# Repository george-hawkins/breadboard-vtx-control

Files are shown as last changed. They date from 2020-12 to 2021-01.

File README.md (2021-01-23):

Breadboard SmartAudio control via OpenTX
========================================

This project is about creating a breadboard setup where a standard STM32 Nucleo development board acts as a flight controller that enables a transmitter, running OpenTX, to control a SmartAudio video transmitter via an FrSky X-series receiver.

Once set up, you can use a LUA script on your transmitter to change the band etc. on the VTX.

Parts used:

* [Nucleo F722ZE](https://www.st.com/en/evaluation-tools/nucleo-f722ze.html) development board.
* [FrSky X8R](https://www.frsky-rc.com/product/x8r/) receiver (RX).
* [Eachine TX805](https://www.eachine.com/Eachine-TX805-5_8G-40CH-25-or-200-or-600-or-800mW-FPV-Transmitter-TX-LED-Display-Support-OSD-or-Pitmode-or-Smart-Audio-RP-SMA-Female-p-1234.h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) video transmitter (VTX).
* [Eachine 1000TVL](https://www.eachine.com/Eachine-1000TVL-1-3-CCD-110-Degree-2.8mm-Lens-Mini-FPV-Camera-NTSC-PAL-Switchable-p-357.html) FPV camera.
* [12V power supply](https://www.reichelt.com/de/en/eco-friendly-plug-in-power-supply-unit-12-v-1500-ma-2-5-mm-snt-1500-12v-2-5-p108993.html) (plus barrel jack to terminal block [adapter](https://www.adafruit.com/product/368)).

All the work below was done using a computer running Ubuntu, but it should be easy enough to adapt things for Mac or Windows.

Wiring
------

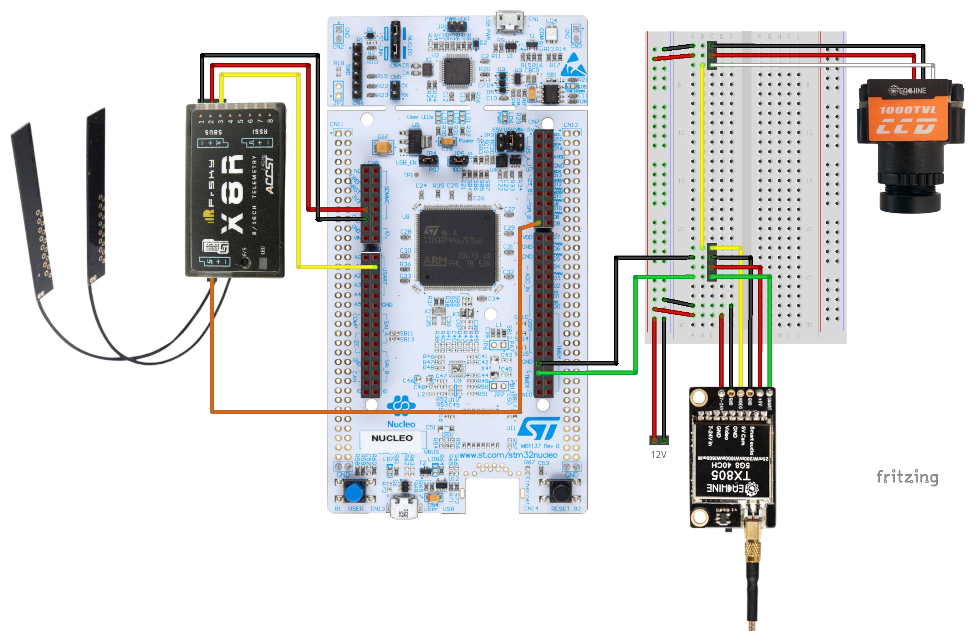
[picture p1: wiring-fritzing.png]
wiring with Fritzing


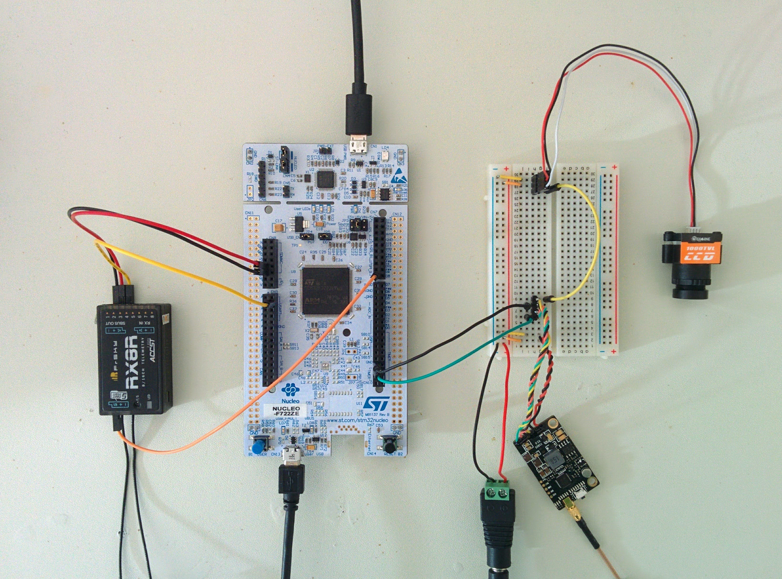
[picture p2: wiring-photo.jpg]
wiring photo


Setting up the Nucleo board
---------------------------

The NUCLEO F722ZE has two USB ports - one, labeled _CN1_, on the small subboard at one end and one, labeled _CN13_, on the main board at the other end. The small subboard is the builtin [ST-LINK](https://www.st.com/en/development-tools/st-link-v2.html). 

Aside: Oddly, the two USB connectors use different components - the one on the ST-LINK is clearly a micro-USB connector, the other is also a micro-USB but upside-down relative to the other one.

Plug a USB cable into the ST-LINK connector (plugging it into the other one does nothing due to the default jumper settings) - it appears as a USB drive.

The board comes with a pre-installed example application that will flash the red user LED madly, press the button labeled _USER_ to get it to cycle through the other user LEDs.

### Upgrade the ST-LINK firmware

Find the latest ST-LINK upgrader under the [products section](https://www.st.com/en/development-tools/stm32-programmers.html#products) of STM32 Programmers page. At the time of writing, it was [STWS-LINK007](https://www.st.com/en/development-tools/stsw-link007.html).

Aside: ST's package naming is quite odd, e.g. at the present time STWS-LINK007 is a package for upgrading the firmware of an ST-LINK device while STSW-LINK009, which sounds like a more recent revision of the same, is in fact a package for the USB drivers needed by Windows to work with an ST-LINK device.

Register with the ST site, download the application and run the upgrader:

    $ cd Downloads
    $ unzip en.stsw-link007_V2-37-26.zip 
    $ cd stsw-link007
    $ cd AllPlatforms
    $ command -v java
    .../bin/java ...
    $ sudo .../bin/java -jar STLinkUpgrade.jar

Note: if you've got the Arduino IDE installed, it includes a version of Java that you can use - you can find `java` in the `java/bin` subdirectory of the IDE's main installation directory.

`sudo` is required so that the application can open USB devices. Once started, the GUI should detect the board, click the _Open in update mode_ and click _Upgrade_ if the _Version_ shown isn't the same as the one shown for _Update to Firmware_.

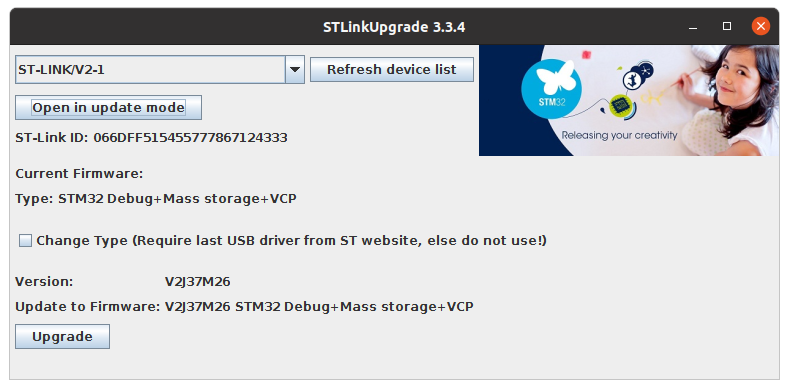
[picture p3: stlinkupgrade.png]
STLinkUpgrade


Note: the ST-LINK upgrader is bundled with the [STM32CubeIDE](https://www.st.com/en/development-tools/stm32cubeide.html) (along with a suitable JRE) - once you've installed and started the IDE, you can find the upgrader as _ST-LINK Upgrade_ in the _Help_ menu.

Installing Betaflight
---------------------

After Betaflight has been installed for the first time, it can be updated via the [Betaflight Configurator](https://github.com/betaflight/betaflight-configurator). But to install it for the first time you have to use the USB drive that shows up when you connect to the ST-LINK subboard via USB (as described above). But first let's build Betaflight locally...

### Building Betaflight

Clone the Betaflight repository:

    $ git clone git@github.com:betaflight/betaflight.git
    $ cd betaflight

Checkout the latest [tag](https://github.com/betaflight/betaflight/tags):

    $ git checkout 4.2.5

The Betaflight Ubuntu build instructions are [here](https://github.com/betaflight/betaflight/blob/master/docs/development/Building%20in%20Ubuntu.md).

It says the first things you should do is:

    $ make arm_sdk_install

All this does is download a tarball for `gcc-arm-none-eabi` into the `downloads` directory and then unpacks it into the `tools` directory.

However, instead of this we can just get `apt` to do this for us:

    $ sudo apt install gcc-arm-none-eabi

Aside: if you've used `gcc-arm-none-eabi` before, you may be wondering if you should be installing it via a non-standard PPA. If you're running a recent version of Ubuntu, e.g. 20.04 LTS, then the answer is no. See the [_Notes_](#notes) section below for more details.

Now, it's trivial to build an image suitable for installation on the Nucleo board:

    $ make hex TARGET=NUCLEOF722
    ...
    Creating HEX ./obj/betaflight_4.2.5_NUCLEOF722_afdac08b3.hex
    ...

This makes a hex image for the `NUCLEOF722` target. You can find all possible targets like this:

    $ ls src/main/target
    AG3X  BEEBRAIN_V2F  CRAZYFLIE2  ...

If you want to remove all the object files etc.:

    $ make clean TARGET=NUCLEOF722

Note: if you omit `TARGET=NUCLEOF722` then it will just try to remove object files, and the like, associated with the default target (which, fairly arbitrarily, is set to `STM32F405`).

The `make` output above showed that it created the hex file `/obj/betaflight_4.2.5_NUCLEOF722_afdac08b3.hex`:

    $ ls -sh obj/betaflight_4.2.5_NUCLEOF722_afdac08b3.hex
    1.2M obj/betaflight_4.2.5_NUCLEOF722_afdac08b3.hex

Now install the hex file on the board - this simply requires copying it to the board's USB drive:

    $ cp obj/betaflight_4.2.5_NUCLEOF722_afdac08b3.hex /media/$USER/NODE_F722ZE

The drive unmounts and remounts. After remounting and going through a boot sequence, the board's red and green LEDs are lit and the blue LED flashes on and off.

Note: sometimes the `cp` completes without any obvious error but Betaflight then doesn't even start its boot process (no LEDs come on at all) - plugging the board in and out and redoing the copy fixes things.

TODO: see if you can instead use the prebuilt STM32F7X2 universal target that Betaflight now releases (e.g. `betaflight_4.2.6_STM32F7X2.hex` [here](https://github.com/betaflight/betaflight/releases/tag/4.2.6) in the 4.2.6 release). It might even be an improvement given the odd invalid UART3 pin definitions in the NUCLEOF722 - one would instead define all UARTs as required using the CLI `resource` command.

### Using Docker to build Betaflight

An alternative to having to set up a suitable development environment, is to install and use [Docker](https://docs.docker.com/engine/install/).

Assuming you've got Docker installed, download this [Dockerfile](Dockerfile) and:

    $ cd betaflight
    $ cp ~/Downloads/Dockerfile .

At any point you can clean everything with:
 
    $ sudo rm -rf downloads obj tools

Aside: why do you need `sudo`? Because the `Dockerfile` creates files with a different user ID to the current user. TODO: fix this.

First step:

    $ docker run --rm --volume $PWD:/betaflight betaflight:latest make arm_sdk_install

Then make sure everything is clean:

    $ docker run --rm --volume $PWD:/betaflight betaflight:latest make clean TARGET=NUCLEOF722

Then build the hex target:

    $ docker run --rm --volume $PWD:/betaflight betaflight:latest make hex TARGET=NUCLEOF722
    $ ls obj/betaflight_4.2.5_NUCLEOF722_afdac08b3.hex

Using Betaflight Configurator
-----------------------------

Now that Betaflight is installed, Betaflight Configurator can be used to configure things.

Download the latest Betaflight Configurator from [releases](https://github.com/betaflight/betaflight-configurator/releases). Then...

    $ mv ~/Downloads/betaflight-configurator_10.7.0_amd64.deb /tmp
    $ cd /tmp
    $ sudo apt install ./betaflight-configurator_10.7.0_amd64.deb

Aside: moving things into `/tmp` just avoids `apt` issues over who owns the containing directory (the user who downloaded the `.deb` file or the root user running `apt install`).

The Configurator ends up in `/opt/betaflight/betaflight-configurator`:

    $ apt list --installed | fgrep -i betaflight
    betaflight-configurator/now 10.7.0 amd64 [installed,local]
    $ dpkg-query -L betaflight-configurator
    ...
    /opt/betaflight/betaflight-configurator/betaflight-configurator
    ...

So far we've been communicating with the board via the USB connector on ST-LINK subboard. However, the Configurator needs to communicate with the board via the other USB connector. So keep the board powered via the ST-LINK and plug in another USB cable to the second USB connector.

The [_Notes_](#notes) section covers creating a `udev` rule for this second USB connector. Assuming you've got it set up such that you don't need to use `sudo` to access it, you can start the Configurator:

    $ /opt/betaflight/betaflight-configurator/betaflight-configurator

If you leave it for a second or two, it automatically detects the correct values for the two serial port related dropdowns left of the _Connect_ button:

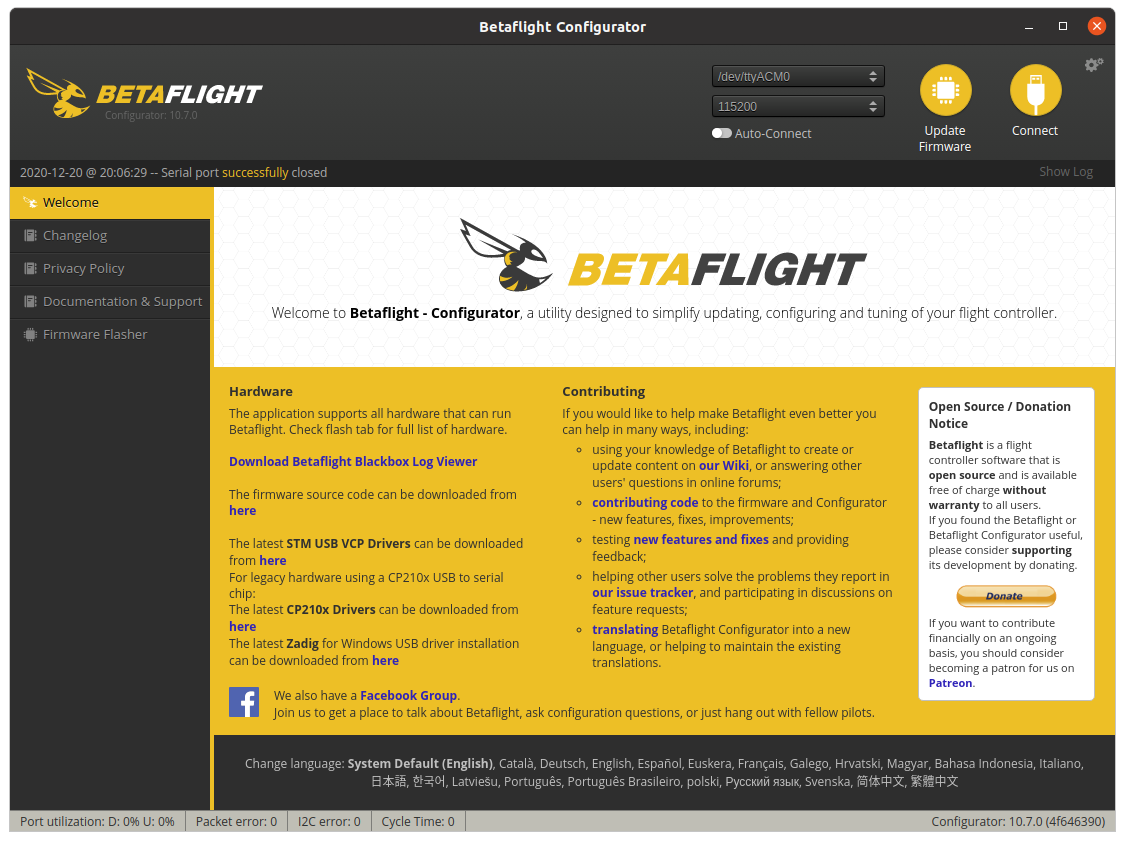
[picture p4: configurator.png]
Configurator


With the `udev` rule you can always see which is the right port:

    $ ls -l /dev/stm-virtual-com 
    lrwxrwxrwx 1 root root 7 Dec  8 17:34 /dev/stm-virtual-com -> ttyACM1

Note: when you power up, restart or reboot the board, you have to wait for the board to fully start up for the Configurator to be able to detect the correct port. The board is ready it turns on the green user LED - when this happens the Configurator almost instantly correctly detects it.

Click the _Connect_ button and ignore the warning about the _motor output protocol_ and the _accelerometer_.

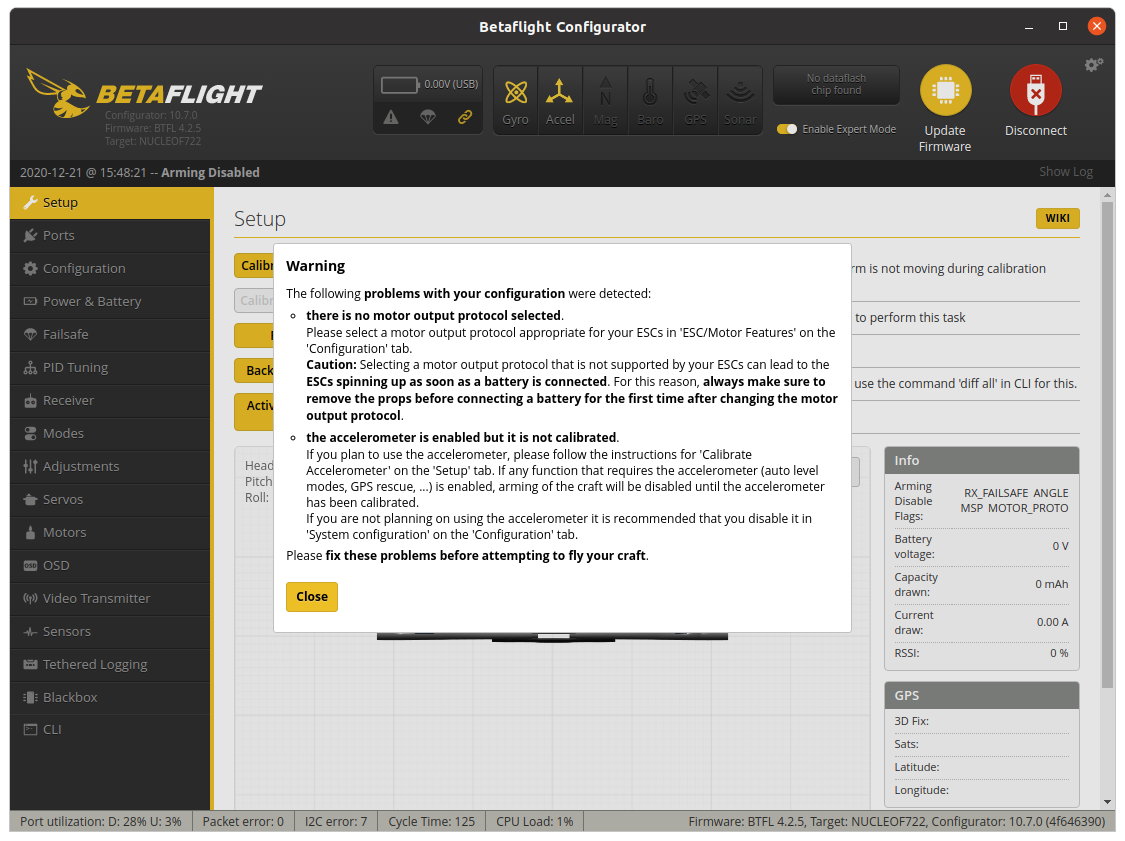
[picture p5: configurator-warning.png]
configurator-warning


Now, if you want to update the firmware, you can do this via the Configurator rather than copying it over via the ST-LINK.

Nucleo pinout
-------------

Now, we're going to start wiring things up to the Nucleo board. To do this we need a pinout diagram for the board's headers (there are the left and right headers and each of these is in turn split into an upper and lower part, these parts are named CN7, CN8, CN9 and CN10).

Unfortunately there don't seem to be any really nice pinout diagrams for the board, the best is the one that you can find in the user manual that you can download from the [documentation section](https://www.st.com/en/evaluation-tools/nucleo-f722ze.html#documentation) of the board's page on the ST site. The diagram in the _Hardware layout and configuration_ section of the manual is just the same as the one that comes in the board's blister pack.

The silkscreen on the board itself isn't very helpful as the pins are laid out to be very similar to the Arduino UNO headers and are given names that correspond to the pin names on the UNO rather than their real STM32 names.

Initially, I referred to some pins here by their silkscreened names but this turns out to be very confusing. E.g. the silkscreened A0 corresponds to the similarly positioned A0 on an Arduino UNO. However, the STM32 also has an A0 pin (referred to as PA0 in the Nucleo manual and as A00 within Betaflight Configurator) that is totally unrelated to this silkscreened pin A0.

**Important:** each header consists of two rows of pins (unlike the Arduino UNO with its single rows) - initially I incorrectly assumed that the two rows were just the same pins doubled up. The pins on the inner and outer rows are completely distinct.

You can find how pins are assigned for a particular Betaflight target in its `target.h` file, in our case this is [`src/main/target/NUCLEOF722/target.h`](https://github.com/betaflight/betaflight/blob/master/src/main/target/NUCLEOF722/target.h). E.g. there, you'll see:

    #define USE_UART2
    #define UART2_RX_PIN PD6
    #define UART2_TX_PIN PD5

So the UART2 RX and TX pins are PD6 and PD5 respectively. If you look at the pinout diagram in the user manual (or the one that came in the board's blister pack), you'll find these pins near the top-right of the CN9 header.

Note: STM produce a very wide range of Nucleo boards but only some of them are listed on the Mbed boards [page](https://os.mbed.com/platforms/?q=&Board+vendor=STMicroelectronics). Those that are, do have nice pinout diagrams, e.g. see the Mbed pages for the [Nucleo-F746ZG](https://os.mbed.com/platforms/ST-Nucleo-F746ZG/) and the [Nucleo-F767ZI](https://os.mbed.com/platforms/ST-Nucleo-F767ZI/). Unforunately, unlike the Nucleo-F722ZE that I've used here, neither of these boards has an existing Betaflight target definition. A Nucleo board that has both a Betaflight target definition and an Mbed page is the [Nucleo-H743ZI2](https://os.mbed.com/platforms/ST-Nucleo-H743ZI2/).

I've copied out the pins on Zio headers, from the Nucleo-F722ZE manual, into [`notes/nucleo-f722ze-zio-header.md`](notes/nucleo-f722ze-zio-header.md) - this makes it more convenient to search for the location of a particular pin.

Setting up the RX
-----------------

Now we know where the UART2 RX pin is - let's use it to connect the RX to the board.

Connect the ground and power pins of the RX's S.BUS port to the 5V and GND pins on the CN8 header and connect the S.BUS signal pin to PD6.

Note: the RX takes 5V and the VTX takes 12V but all signal pins on both are 3.3V safe.

In the Configurator, go to the _Ports_ tab and switch the _UART2_ _Serial RX_ toggle to on. All other settings for _UART2_ should be left unchanged, e.g. the _Configuration/MSP_ toggle should be left unselected, i.e. off.

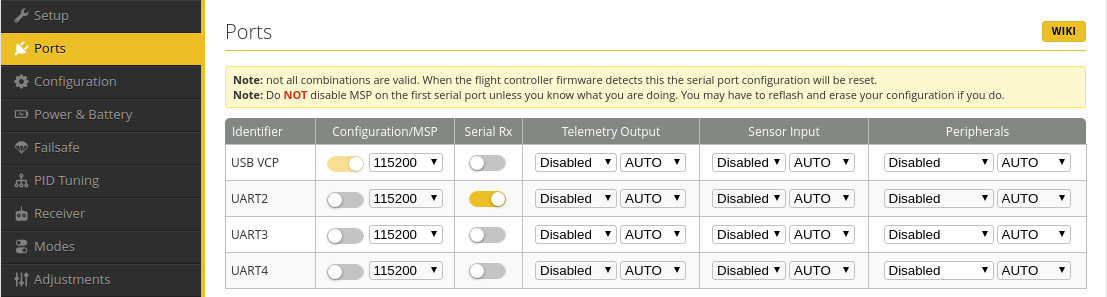
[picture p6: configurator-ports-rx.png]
configurator-ports-rx


Click _Save and Reboot_. Reconnect once the board has rebooted.

Aside: when using the Configurator, it should be fine to make changes on multiple tabs and, once finished with all changes, click _Save and Reboot_. However, I sometimes got the impression that it doesn't always remember unsaved changes from one tab when you switch to another. So in general, I saved changes before switching tabs and always confirmed the changes on reconnecting after the reboot.

**Credit:** these instructions are derived from Oscar Liang's instructions for the F3 [here](https://oscarliang.com/sbus-smartport-telemetry-naze32).

Note: Oscar mentions settings in the _Receiver_ section of _Configuration_ but for this setup they already had the appropriate values.

TODO: note that they're already setup because target.h specifies:

```
#define DEFAULT_RX_FEATURE      FEATURE_RX_SERIAL
#define SERIALRX_PROVIDER       SERIALRX_SBUS
```

Binding the RX 
--------------

On my OpenTX transmitter, I created a new model - all I did was give it a name and bound it to the RX as described [here](https://george-hawkins.github.io/arf-drone/docs/binding).

No other settings are needed but to stop the transmitter complaining about no failsafe being set when it starts up, go to the model's _SETUP_ page, scroll to _Failsafe_ and set it to _No pulses_ (which, with a real drone, would mean you then need to configure how to respond to a failsafe situation on the flight controller itself).

Once the transmitter is bound to the RX, go to the _Receiver_ tab in the Configurator and confirm that the bars move as you move the sticks on the transmitter.

Telemetry
---------

Now, we're going to set up telemetry, i.e. connect a pin on the board to the signal pin of the RX's S.PORT connector and configure the flight controller to output telemetry data on this pin.

Rather than a real UART we're going to use SoftSerial for this.

For SoftSerial we first need a pin for it to use (for telemetry, we only need a TX pin), the usual thing to do is to steal a pin from something that isn't being used. With the Nucleo board there are lots of pins that aren't assigned to anything which could probably be used instead. But we'll do things the normal way and steal a currently assigned pin.

In Configurator, go to the CLI and:

    # resource
    ...
    resource MOTOR 5 E06
    resource MOTOR 6 B04
    resource PPM 1 B15
    ...

The pins suggested for stealing in Oscar's [guide](https://oscarliang.com/betaflight-resource-remapping/) are `LED_STRIP`, `PPM` and spare motor outputs. There's no `LED_STRIP` resource for this board so let's use the last motor output, i.e. `MOTOR 6` (not that we're intending to ever use 1 to 5).

First free it (this isn't really necessary, but it stops Betaflight complaining when we reassign the pin next):

    # resource MOTOR 6 none
    Resource is freed

And assign it to SoftSerial and save:

    # resource SERIAL_TX 11 B04
    Resource is set to B04
    # save

Note: SoftSerial port number starts from 11, `SERIAL_TX 11` being SoftSerial #1 and 12 being SoftSerial #2.

Once it has rebooted and you've reconnected go to the _Configuration_ tab and under _Other Features_ turn on _SOFTSERIAL_ and _Telemetry_.

After _Save and Reboot_ go to _Ports_ and _SOFTSERIAL1_ should now be there (Oscar's guide suggest further steps if _SOFTSERIAL1_ does not show up but these were not necessary).

Now, set the _Telemetry Output_ value for _SOFTSERIAL1_ to _SmartPort_ and _Save and Reboot_.

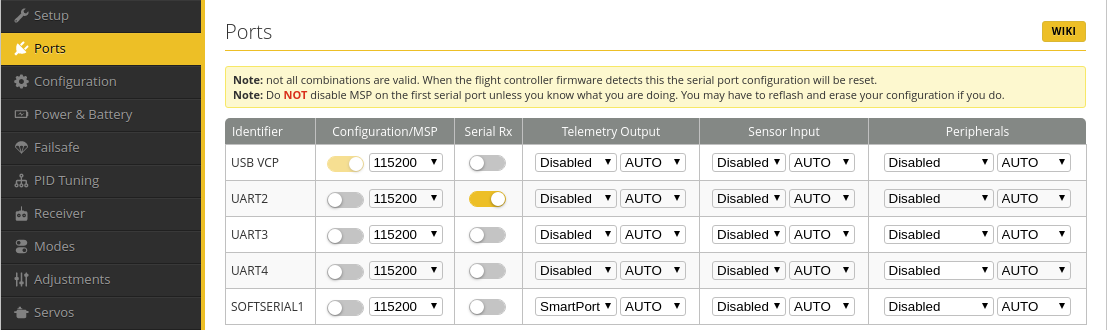
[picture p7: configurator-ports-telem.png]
configurator-ports-telem


Note: there are various other option, in addition to _SmartPort_, in the telemetry dropdown. One of them is _FrSky_ - this refers to an older telemetry protocol used by FrSky receivers before they invented _SmartPort_.

Once everything is set up, connect the S.PORT signal pin of the RX to pin PB4 on the Nucleo board (the bottom-left pin on header CN7).

Note: using `resource` above the pin is called B04, but this isn't the name used in the Nucleo user manual or in `target.h`. Mapping between the two naming conventions is simple enough, e.g. take `B04`, knock out any leading zeros to get B4 and then prepend "P" to get PB4.

After a lot of experimenting, I finally got telemetry working by going to the _CLI_ tab and entering:

    # set tlm_inverted=OFF
    # set tlm_halfduplex=ON
    # save

It turns out that these are actually the default values and it was changing them (according to the instructions of various online tutorials) that had caused my problems.

After this, I could go to the _TELEMETRY_ page for my model, on my transmitter, and select _Discover new sensors_. In addition to RSSI and RxBt (which come directly from the RX and are available even if telemetry hasn't been set up as described above), it discovered an array of additional sensors - i.e. all those listed [here](https://github.com/betaflight/betaflight/blob/master/docs/Telemetry.md#available-sensors) for Betaflight.

Note: the setting `tlm_inverted` seems a little confusing. The S.PORT signal is an inverted serial signal and F3 and F7 STM32 MCUs can handle this inversion but MCUs like the F4 require and external inverter. So `tlm_inverted` is not about the inverted nature of the underlying S.PORT signal but about whether it has been inverted again (to become uninverted) by an external inverter. For this F7 based board an external inverter is unnecessary so `tlm_inverted` is set to `OFF`.

Hardware UART pins
------------------

You can skip over this section, it just covers my experimentation with hardware UART pins.

With an MCU like the ESP32, almost every pin can be used as a UART pin. However, with this STM32 MCU, you don't appear to have much (any?) freedom when it comes to to assigning pins to UARTs. I couldn't work out the scheme to what is and isn't allowed.

In `target.h` various pins are assigned to UARTs 5, 6, 7 and 8 but those UARTs are not actually enabled.

Of the pins assigned to those UARTs, only pins PE8 (TX) and PE7 (RX) of UART7 and pin PE0 (RX) of UART8 are actually pins exposed via the Nucleo header.

Of the UARTs that are actually enabled, i.e. UART2, UART3 and UART4, only pins PD6 (RX) and PD5 (TX) of UART2 and pin PA0 (TX) of UART4 are exposed.

I could use the RX and TX pins of UART2 and the TX pin of UART4 without issue. However, I could not e.g. use PE8 by reassigning it to UART3. This _may_ be because UART3 is used for ST-LINK (search for _USART3_ in the F722ZE manual) - this assumes there's some connection between Betaflight's UART numbering and the devices of the MCU but I don't believe there is.

**Update:**

* "This _may_ be because UART3 is used for ST-LINK" - this isn't the issue, the issue is that the pins must be defined in `target.h` (see below for more details).
* "this assumes there's some connection between Betaflight's UART numbering and the devices of the MCU but I don't believe there is." - I was incorrect, there is a one-to-one correspondance between the numbering in Betaflight and the devices of the MCU.

I also tried reassigning UART4 TX to other pins but this didn't work either.

In the manual's _Hardware layout and configuration_ section for the F722ZE, the pins PD6 and PD5 are described as being the RX and TX pins of _USART_2_ and indeed are used as the RX and TX pins of UART2 in `target.h`.

However, the only other pins described as _USART_ pins, in the manual, are PG14 (TX) and PG9 (RX) for _USART6_ (notice the inconsistent naming _USART_2_ vs _USART6_) and these pins are out of bounds to the Betaflight CLI as it doesn't recognise pin names above F15.

**Update:** it turns out that the range of pins that Betaflight recognises for a particular target is controlled by the `TARGET_IO_PORTA` etc. defines in the target's `target.h` file, the NUCLEOF722 target simply has no `TARGET_IO_PORTG` define, so G pins are not recognised.

The PA0 pin, i.e. UART4 TX, is not described as a UART pin in the F722ZE manual - there it's described as having signal name `TIMER_C_PWM1` and function `TIM2_CH1`.

So one might imagine that a pin with a similar name and function, e.g. PB0 (with signal name `TIMER_D_PWM1` and function `TIM3_CH3`), could be substituted for PA0 but it cannot. Neither can PE9 (`TIMER_A_PWM1` and `TIM1_CH1`) nor PE8 (assigned to UART7 TX in `target.h`).

I tried reassigning PA0 to UART3, but it doesn't work there. And I tried assigning it to SoftSerial (replacing B04 used above) and that didn't work there either.

One might imagine that despite seeming to be able to set `resource` values for UARTs via the CLI that this doesn't actually change anything. However, this is not the case - changes to UART pins via `resource` do affect things, e.g. if you assign PA0 to UART3 but leave _SmartPort_ set for UART4 (and nothing set for UART3), it's not the case that things keep on working, i.e. it's not that under the covers UART4 is still really using PA0 as if it hadn't been reassigned to UART3.

So what exactly the rules are here is quite unclear.

**Update:** pins that are going to be used for motors, ppm, pwn and other purposes (e.g. soft serial) have to be defined in the `timerHardware` table in the target's `target.c` file. UART pins do _not_ have to be defined in this file but perhaps they do have to have been specified as UART pins (with `#define UART2_RX_PIN` etc.), for an enabled UART, for them to be configured such that they're really useable. I.e. you can't just use arbitrary pins names via the CLI that were not in some way configured in the compiled code.

**Update 2:** it turns out you are not free to reassign UART pins via the CLI `resource` command. You must define the pins in `target.h` and you must use the appropriate pins defined in the MCU's datasheet, e.g. <https://www.st.com/resource/en/datasheet/stm32f722ze.pdf> for the STM32F722ZE. For each UART between one and four pins are specified for the RX pin and for the TX pin, you can choose between any of the specified pins for a paricular UART. Often there seems to be a natural grouping, e.g. PD6 and PD5 are RX and TX pins respectively that can be used for UART2, however, this apparent grouping isn't important - e.g. PA3 is another option for the RX pin and it can be used in combination with PD5 as the TX pin. The UART names in the Betaflight code do (and must) match those in the MCU datasheet, e.g. `UART2_RX_PIN` in Betaflight can only be assigned values that are specified as RX pins for UART2 in the datasheet.

**Update 3:** rather than looking at the MCU datasheet, you can find the legal pin options in `src/main/drivers/serial_uart_stm32f7xx.c` (or the appropriate file for your MCU).

TODO: there's a section on UARTs in [`notes/betaflight.md`](notes/betaflight.md) - it should be merged with this section and the whole thing cleaned up.

Telemetry on a hardware UART TX pin
-----------------------------------

Having set up telemetry via SoftSerial, I also wanted to see that it worked the same way using a hardware UART TX pin.

After all the experimentation covered in the previous section (on hardware UART pins), it turns out that only PA0 - the TX pin for UART4 - works.

It was trivial to swap the _SmartPort_ telemetry setting from the SoftSerial port to UART4 using the Configurator and switch the telemetry hookup wire from pin PB4 to PA0 (near bottom-left of CN10).

Using a hardware UART doesn't introduce any increased flexibility with regards `tlm_halfduplex` and `tlm_inverted` - they have to be the same values as they were above for SoftSerial.

SmartAudio
----------

I could connect the RX directly to the Nucleo board. Setting up the VTX and camera involved a bit more set up and a breadboard as the VTX requires 12V and involves rather more pins.

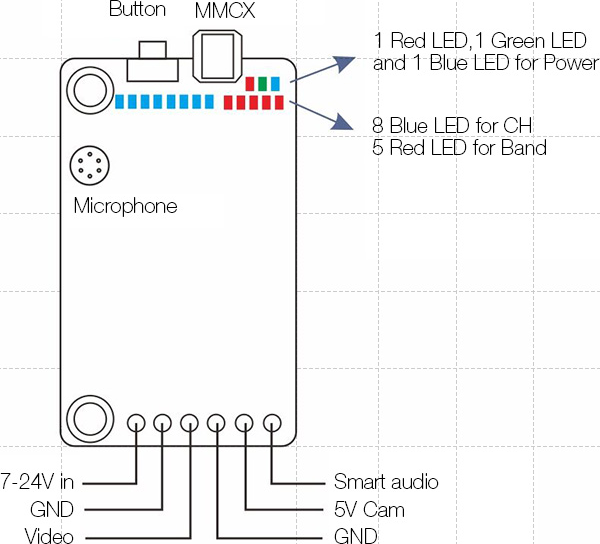
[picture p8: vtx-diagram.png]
vtx-diagram


**Important:** always connect the aerial of a VTX before you power it up - if you don't the VTX will quickly overheat and power itself off (if you're lucky) or burn itself out.

I connected the red and black _voltage-in_ wires to power provided via a 12V adapter. I also connected the FPV camera to the 12V supply. Often, you can power the camera directly off the VTX (see the _5V Cam_ and _GND_ pins in the diagram). However, this camera could handle 12V and it wasn't clear to me that the VTX could definitely provide enough current for this particular camera.

Note: the VTX defaulted to outputting at 600mW (blue LED on). At this power level the VTX very quickly becomes extremely hot, i.e. hot enough to be painful to touch. Switching it down to 25mW brings it within legal limits (and is anyway the nice thing to do in a non-outdoors situation where you don't want to interfere with your neighbor's WiFi). At 25mW, it runs substantially cooler.

I connected the _Video_, _GND_, _5V Cam_ and _SmartAudio_ wires to a small piece of male header and plugged that into the breadboard. Then, via the breadboard, I connected the video signal from the camera to the _Video_ pin of the VTX.

Aside: with a proper flight controller, you'd connect the video pin of the camera to the flight controller and then connect the flight controller to the VTX - this would allow the flight controlled to overlay what's called an OSD (on-screen display) onto the video signal. However, the Nucleo board has no OSD hardware, so it cannot do this.

Then (after restoring telemetry to SoftSerial pin PB4) I connected the SmartAudio pin on the VTX to pin PA0 on the Nucleo board, i.e. the UART4 TX pin. And I connected the _GND_ pin (beside _5V Cam_) to a ground pin on the Nucleo board - conveniently there's one just above the PA0 pin.

**Important:** initially, I didn't connect the VTX ground pin to a ground pin on the Nucleo board. I didn't think this was necessary - I naively assumed that as the 5V source for the Nucleo board and the 12V power adapter were both ultimately powered off the same A/C source that they would have the same ground. This is not the case - relative to the ground of the Nucleo board the voltage seen when connecting the SmartAudio pin the Nucleo board was permanently at around 3.3V (it's not possible for me to tell if it was above 3.3V, just that it was at the max, luckily the pins involved were not damaged) rather than an oscillating signal going between 0 and 3.3V. After a lot of frustration, it simply required connecting the ground pins as described to resolve this issue.

Then, once things were wired up, I followed Oscar Liang's [guide](https://oscarliang.com/vtx-control/) and set things up in the Configurator:

* Under the _Ports_ tab, I set the _Peripherals_ drop down for _UART4_ to _VTX (TBS SmartAudio)_ (and clicked _Save and Reboot_).
* Under the _Other Features_ section of the _Configuration_ tab, I toggled _OSD_ to on (and clicked _Save and Reboot_).

The second step proved pointless - as mentioned above the OSD depends on the video signal being routed via a flight controller that has the necessary OSD hardware.

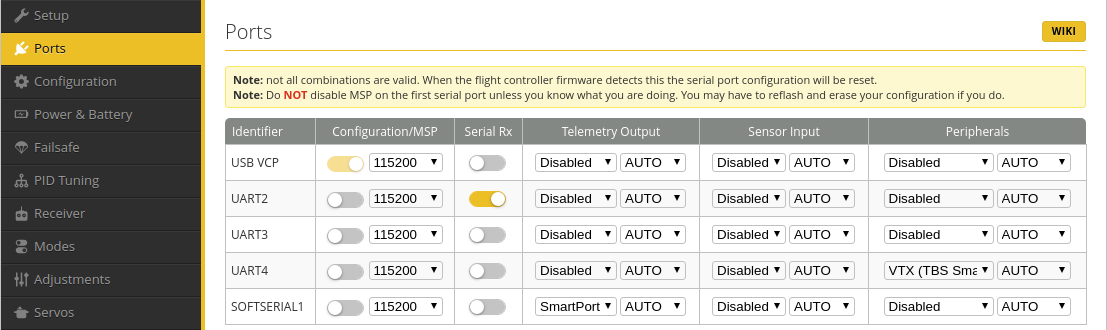
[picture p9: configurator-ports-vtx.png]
configurator-ports-vtx


Then continuing with Oscar's guide I went about setting up the _VTX table_. First, I determined the SmartAudio version using the Configurator (as described in the video linked to from the Betaflight _VTX Tables_ [wiki page](https://github.com/betaflight/betaflight/wiki/VTX-tables)) like so:

* Under the _Blackbox_ tab, I set the _Blackbox debug mode_ to _SMARTAUDIO_ (and clicked _Save and Reboot_).
* Then I toggled _Enable Expert Mode_ to on (it's to the left of the _Update Firmware_ and _Connect_ buttons).
* Then under the _Sensors_ tab, I unselected everything already selected (_Gyroscope_ and _Accelerometer_) and selected only _Debug_.

The value I saw for _Debug 0_ was 216 - which correspond to the value for "SA 2.0 unlocked" shown in the wiki page (rather than the values mentioned in the video).

**Note:** if PR [#10413](https://github.com/betaflight/betaflight/pull/10413) (and its related Configurator PR) are merged, you'll be able to see the SmartAudio version directly in the VTX tab without all this debug stuff.

Aside: see the [_Notes_](#notes) for more on the values that you see in the _Debug 1_ and _Debug 2_ channels.

So given that my VTX is SmartAudio 2.0, I downloaded the _SmartAudio 2.0 (EU)_ JSON file from the _VTX Tables_ wiki page and loaded it in the Configurator by going to the _Video Transmitter_ tab, selecting _Load from file_ and, once it was loaded, selecting _Save_.

It looks like, in the EU, you can't have frequencies below around 5732 and above around 5866, so the top A band channel is unavailable as are the lower two and higher two race band channels (and so show as having value 0). Band E is not legal in the EU, hence it appears as _UNKNOWN_ between bands B and F.

I reduced the number of bands to 5 (and then pressed _Save_) to knock out the I band that isn't mentioned in the TX805 mini-manual. Other than that everything lined up with the table of frequencies in the manual.

By default there's only a 25mW power level, under the bands in the _VTX Table_ section, you can add additional power levels if your VTX supports them (and they're legal in your jurisdiction).

Note: Oscar Liang sets up the VTX table using the CLI - I don't see the need for this as the file based approach works well.

Aside: under _Video Transmitter_ tab, you can select _Save LUA Script_ which saves a file, that describes the frequencies table, which can, apparently, be loaded into OpenTX. However, I don't know why you would do this as the Betaflight script on the transmitter can download this table itself from the flight controller via the RX using the MSP protocol.

Now everything is set up, one can control the VTX via the _Selected Mode_ section of the _Video Transmitter_ tab. E.g. select band _BOSCAM_A_, channel _Channel 1_ and power _25_ and press _Save_ and you'll see the LEDs change accordingly on the VTX.

Bit rates
---------

The final setup above, uses UART2 for S.BUS, UART4 for SmartAudio and SoftSerial1 for S.PORT. Ideally, the hardware serial ports should be assigned to the protocols with the highest bit rates and soft serial used for the lowest bit rate protocol. So what are the bit rates of the various protocols?

* S.BUS - 100kbps
* S.PORT - 57.6kbps
* SmartAudio - 4.8kbps

Aside: S.BUS seems to be completely non-standard - it's inverted and it uses an unusual bitrate (100kbps rather than something more common like 115.2kbps).

SmartAudio uses a significantly lower bitrate than the two FrSky protocols - so really it should have been assigned to SoftSerial1.

Transmitter setup
-----------------

TODO: important - the Betaflight scripts depend on telemetry as the channel for data from the flight controller to the TX. If you haven't already discovered all the sensors (as described above when discussing the _TELEMETRY_ page) then the Betaflight scripts will continuously flash a _No Telemetry_ warning (it actually just checks for the _RSSI_ sensor and assumes if its not present then no telemetry is present - this is odd as the RSSI sensor data comes from the RX rather than the flight controller).

Assuming you've got your transmitter and receiver upgraded to the latest OpenTX firmware releases (in the case of the transmitter and its bootloader) and FrSky firmware releases (in the case of the receiver and the transmitter's internal radio module) then, following the Betaflight TX Lua Scripts [instructions](https://github.com/betaflight/betaflight-tx-lua-scripts#installing), you just need to:

* Download the latest zip file from the releases [page](https://github.com/betaflight/betaflight-tx-lua-scripts/releases).
* Mount the _OPENTX_ SD card and...

```
$ cd ~/Downloads/
$ unzip betaflight-tx-lua-scripts_1.5.0.zip 
$ cd obj
$ cp -r * /media/$USER/OPENTX
$ ls /media/$USER/OPENTX/SCRIPTS/TOOLS
bf.lua ...
```

If `bf.lua` is there, as shown, then all is good.

Aside: `obj` seems an odd name for the root directory of the extracted zip file.

Once the transmitter is restarted, long press _MENU_, this takes you to the _TOOLS_ page. Scroll down and select _Betaflight setup_, the first time it runs it goes through a one-time setup process, once this has happened select _Betaflight setup_ again. Now when you select it, it will display _Downloading VTX tables_ for a while. It does this by communicating with the flight controller using MSP (MultiWii Serial Protocol).

Aside: MSP seems to be rather poorly documented, if you're interested, you can find the protocol described [here](http://www.multiwii.com/forum/viewtopic.php?f=8&t=1516) and the Betaflight implementation [here](https://github.com/betaflight/betaflight/tree/master/src/main/msp).

This line in the [README](https://github.com/betaflight/betaflight-tx-lua-scripts/blob/master/README.md) took me a while to work out:

> If you change the VTX table, you have to re-load the updated VTX table in the script, by choosing the 'vtx tables' option in the function menu.

If you update the VTX tables in Betaflight Configurator then on your transmitter go to _TOOLS_ / _Betaflight setup_ / _VTX Settings_ and then press and hold _ENTER_, this will bring up a popup menu where one of the options is _vtx tables_ - simply select it and the VTX table (with your updates) will be re-downloaded.

You can reach this popup menu (what they call the _function menu_) from any of the subpages of _Betaflight Config_, e.g. _VTX Settings_, _PIDs 1_ etc., but not from the main page itself.

The menu items of the popup are:

* _save page_ - any changes you make on a page, e.g. to the _Band_ etc., are only actually applied after you select _save page_.
* _reload_ - reload the values displayed on the page from the flight controller.
* _reboot_ - reboot the flight controller.
* _vtx tables_ - described above. 

Note: once upon a time it was possible to configure things such that one could interact with the Betaflight script via the OpenTX telemetry screens and this is covered in many existing tutorials. This in no longer possible - you can only access it now via the _TOOLS_ page (as just described) - for more details see issue [#306](https://github.com/betaflight/betaflight-tx-lua-scripts/pull/306). This change came with version 1.5.0 (released in May 2020) of the scripts.

Now everything is set up, you can change _Band_ etc. under _VTX Settings_. As already noted, your changes only come into effect when you long press _ENTER_ and select _save page_. You can change everything except the _Protocol_ value (which is set to _SA_, i.e. SmartAudio).

Aside: once this is all set up, one essentially gives up the ability to configure the VTX by its push button. You can still change VTX settings via the push-button but then, in OpenTX, if you press _reload_ via the _function menu_, nothing changes. And if you reboot the flight controller it will restore the settings on the VTX to those seen under _VTX Settings_. So it seems that while there is two-way communication between the flight controller and the transmitter, the flight controller only sets values for the VTX but doesn't try to read them. As we saw above, we can read the Smart Audio version from the VTX so there does seem to be two-way communication between the flight controller and the VTX - but the flight controller simply doesn't use this capability to update its values, for band etc., to values set via the VTX.

Note: if you're on the Configurator _Video Transmitter_ tab and you change the settings via OpenTX then you have to switch to another Configurator tab and then back to _Video Transmitter_ to force it to load the changes - the Configurator has no equivalent of the OpenTX _reload_ menu option.

See the [_Notes_](#notes) for a discussion of pit mode, i.e. the ultra-low power mode that's below even 25mW.

Conclusion
----------

That's it. Now, you can control the VTX via the transmitter. The following sections are just some additional documentation and notes.

There are also further notes in the [`notes`](notes) subdirectory.

X8R ports
---------

For this setup, we're just interested in the S.PORT and the S.BUS ports. You can see which are the plus, minus and signal pins in the little graphic for each port on the top of the RX.

X8R ports

TX805 manual
------------

The TX805 doesn't come with much of a manual and some of it is a bit incoherent or just incorrect (e.g. the power pins LEDs stay lit rather than flickering on and then off). And oddly Eachine doesn't make its manuals available for download as PDFs - so here is a (rather poor) scan of it:

tx805-manual

Notes
-----

Miscellaneous notes related to various things above.

### Full chip erase

If you get your board into a state where you can no longer connect to it via the Betaflight Configurator you can do a full chip erase and then copy a known good firmware onto the board.

You can do a full chip erase (and lots of other things) with the [STM32CubeProgrammer](https://www.st.com/en/development-tools/stm32cubeprog.html). Download and install it (`sudo` is not needed):

```
$ cd ~/Downloads
$ mkdir en.stm32cubeprg-lin_v2-6-0
$ cd en.stm32cubeprg-lin_v2-6-0
$ unzip ../en.stm32cubeprg-lin_v2-6-0.zip 
$ ./SetupSTM32CubeProgrammer-2.6.0.linux 
```

Note: it asks you if you want to install entries for it in your Start Menu and on your Desktop - but the Linux version installed files that I think are intended for Ubuntu Unity, which is pointless on a modern Ubuntu release running Gnome.

To run it you have to be in the programmer's `bin` directory (otherwise it can't connect and you get an "Unable to list supported devices" error, the solution of being in the `bin` directory comes from this forum [answer](https://community.st.com/s/question/0D53W00000FQK5vSAH/stm32cubeprogrammer-unable-to-list-supported-devices)). So:

```
$ cd ~/STMicroelectronics/STM32Cube/STM32CubeProgrammer/bin
$ ./STM32CubeProgrammer
```

Then click _Connect_ to connect to the board and then press _Full chip erase_ (it's just above the help icon that's bottom-left). Click the hamburger icon (top-left) so see full names for the various icons along the left-hand side. There's also a _Full chip erase_ button in the _Erasing & programming_ tab.

Note: there's also something called `cubeprogrammer` bundled with the STM32CubeIDE but I don't know how or if one can access it directly or if it just provides the programmer functionality used when you run programs on your device. Your can find it like so:

    $ ls /opt/st/stm32cubeide_*/plugins/*cubeprogrammer*.jar

It's not an executable jar.

### Creating a udev rule for the Nucleo board

If you're already a member of the `dialout` group, you may well not need to do anything special to be able to access the non-ST-LINK USB port on the Nucleo board.

But let's go through creating a comprehensive rule for the board. First we need the details that are output to `syslog` when the USB cable is plugged in:

    $ tail -f /var/log/syslog
    Dec  8 17:11:52 systemd[1490]: Started VTE child process 30338 launched by gnome-terminal-server process 2758.
    Dec  8 17:15:03 kernel: [12304.704318] usb 3-4.4: new full-speed USB device number 10 using xhci_hcd
    Dec  8 17:15:03 kernel: [12304.806319] usb 3-4.4: New USB device found, idVendor=0483, idProduct=5740, bcdDevice= 2.00
    Dec  8 17:15:03 kernel: [12304.806322] usb 3-4.4: New USB device strings: Mfr=1, Product=2, SerialNumber=3
    Dec  8 17:15:03 kernel: [12304.806323] usb 3-4.4: Product: STM32 Virtual ComPort in FS Mode
    Dec  8 17:15:03 kernel: [12304.806323] usb 3-4.4: Manufacturer: Betaflight
    Dec  8 17:15:03 kernel: [12304.806324] usb 3-4.4: SerialNumber: 3986356B3037
    Dec  8 17:15:03 kernel: [12304.814015] cdc_acm 3-4.4:1.0: ttyACM1: USB ACM device
    Dec  8 17:15:03 mtp-probe: checking bus 3, device 10: "/sys/devices/pci0000:00/0000:00:14.0/usb3/3-4/3-4.4"
    Dec  8 17:15:03 mtp-probe: bus: 3, device: 10 was not an MTP device
    Dec  8 17:15:03 snapd[691]: hotplug.go:199: hotplug device add event ignored, enable experimental.hotplug
    Dec  8 17:15:03 mtp-probe: checking bus 3, device 10: "/sys/devices/pci0000:00/0000:00:14.0/usb3/3-4/3-4.4"
    Dec  8 17:15:03 mtp-probe: bus: 3, device: 10 was not an MTP device
    Dec  8 17:15:06 ModemManager[779]: <info>  Couldn't check support for device '/sys/devices/pci0000:00/0000:00:14.0/usb3/3-4/3-4.4': not supported by any plugin

This shows that both the `ModemManager` and `mtp-probe` try to access the device. We want a rule that:

* Tells `ModemManager` and `mtp-probe` to ignore the device.
* Makes the device accessible by any user without using `sudo`.
* Creates a soft-link to the device with the name `stm-virtual-com`.

Even if one doesn't use the soft-link directly, e.g. in Betaflight Configurator, it's always useful to be able to see which `/dev` file has been assigned to our device when it's plugged in:

    $ ls -l /dev/stm-virtual-com 
    lrwxrwxrwx 1 root root 7 Dec 21 14:00 /dev/stm-virtual-com -> ttyACM0

The important line in the log output that identifies the device is:

    kernel: [12304.806319] usb 3-4.4: New USB device found, idVendor=0483, idProduct=5740, bcdDevice= 2.00

If you look up the `idVendor` and `idProduct` values [here](https://usb-ids.gowdy.us/read/UD/) on the USB ID repository you can see that this is a virtual COM port from ST.

Using these values, we can now create a rule for the device:

    # ST - virtual COM port.
    SUBSYSTEM=="tty", ATTRS{idVendor}=="0483", ATTRS{idProduct}=="5740", \
        SYMLINK+="stm-virtual-com", MODE="0666"

    ATTRS{idVendor}=="0483", ATTRS{idProduct}=="5740", ENV{ID_MM_DEVICE_IGNORE}="1"

    ATTRS{idVendor}=="0483", ATTRS{idProduct}=="5740", ENV{MTP_NO_PROBE}="1"

Just create a file called `/etc/udev/rules.d/50-serial-ports.rules` containing these lines or, if the file already exists, just copy them into the file. There's nothing important about the file's name, what's important is that it exists under `/etc/udev/rules.d` and that it conforms to the naming convention `<number>-<name>.rules` (where `<number>` is anything from `00` to `99`).

That's it - nothing needs to be restarted or informed about these changes - they'll be read next time a device is plugged in.

### GNU Arm Embedded Toolchain

Many older tutorials on ARM development cover adding an additional PPA in order to install `gcc-arm-none-eabi`.

Originally, the latest version of `gcc-arm-none-eabi` was released via a PPA maintained by [Terry Guo](https://launchpad.net/~terry.guo).

Then in late 2015, releases were moved to the "GCC Arm Embedded Maintainers" team PPA (see this [announcement](https://launchpad.net/gcc-arm-embedded/+announcement/13824)).

However, no new releases have been made available via this PPA since 2018 (the last release being for 18.04 LTS).

In 2016, ARM decided to move from using Lauchpad to managing everything from arm.com domains (see this [announcement](https://launchpad.net/gcc-arm-embedded/+announcement/14244)).

The main site for the toolchain is now the GNU Arm Embedded Toolchain [subsite](https://developer.arm.com/tools-and-software/open-source-software/developer-tools/gnu-toolchain/gnu-rm) on Arm Developer.

And finally, the `gcc-arm-none-eabi` [package](https://packages.ubuntu.com/focal/gcc-arm-none-eabi) available for Focal (20.04 LTS) and later releases, via the standard Ubuntu PPAs, is based directly on the packages released by ARM and there is no longer any need to add any additional PPA in order to install it.

### Minor Betaflight issue

Betaflight Configurator allows you to e.g. configure _Serial RX_ and _SmartPort_ on a single UART but this doesn't work. S.BUS and S.PORT use different bit rates so this is hardly surprising. When you reboot the board the _SmartPort_ becomes unset if you tried to set it on a port already configured for _Serial RX_ but ideally Configurator would stop you doing this kind of thing in the first place.

### Voltages

I don't really understand why connecting ground pins on the VTX and Nucleo board  works. If the ground of one source is higher than the ground of the other why does ground level out when the grounds of the two sources are connected? And why doesn't the 3.3V of one source remain raised relative to the other ground, i.e. look like something greater that 3.3V to things connected to the other source.

Note that the Nucleo manual clearly says:

> Caution:1 The I/Os of STM32 microcontroller are 3.3 V compatible instead of 5 V for ARDUINO&reg; Uno V3.

### SmartAudio debug channels

Above, the SmartAudio version was determined using the _Debug 0_ channel. Oscar's summary of the values in this [post](https://intofpv.com/t-what-smartaudio-version-do-i-have) also covers what you see in the _Debug 1_ and _Debug 2_ channels.

If I adjust the band on the VTX then I see the following _Debug 1_ values depending on the band:

* Band = 1, Debug 1 = 0
* Band = 2, Debug 1 = 15
* Band = 3, Debug 1 = 23
* Band = 4, Debug 1 = 31
* Band = 5, Debug 1 = 39

Changing the channel should have changed the output of _Debug 2_, but it seemed to stay stuck at just one value.

### Retrieving values via the Betaflight CLI

You can just enter part of a value name and get all values containing that substring:

    # get vtx_
    osd_vtx_channel_pos = 234
    Allowed range: 0 - 15359

    vtx_band = 1
    Allowed range: 0 - 8
    Default value: 0

    vtx_channel = 1
    Allowed range: 0 - 8
    Default value: 0

    vtx_power = 1
    Allowed range: 0 - 7
    Default value: 0

    vtx_low_power_disarm = OFF
    Allowed values: OFF, ON, UNTIL_FIRST_ARM

    vtx_freq = 5865
    Allowed range: 0 - 5999
    Default value: 0

    vtx_pit_mode_freq = 0
    Allowed range: 0 - 5999

    vtx_halfduplex = ON
    Allowed values: OFF, ON

### Pit mode

Strangely, it doesn't seem to be possible to configure the VTX to start in pit mode without going via the OSD (which our setup doesn't have).

My VTX is a SmartAudio 2.0 device, it was only with SmartAudio 2.1 that it became possible to actively enter pit mode, previous to that you could only configure the device such that it would start in pit mode.

To do this one should set `RACE` mode (not to be confused with the race band) via the OSD as described [here](https://github.com/betaflight/betaflight/wiki/Unify-Smartaudio#op-model). According to some sources you have to power cycle the VTX straight after setting the `OP MODEL` to `RACE` or it'll be forgotten.

However, as this setup doesn't have an OSD, this isn't possible. Oddly, while one can do nearly everything, that one can do via the OSD, using the CLI or Configurator, it doesn't seem possible to set the `OP MODEL`. I've asked about this on RcGroups [here](https://www.rcgroups.com/forums/showthread.php?3787149) and on the Betaflight Slack channel [here](https://betaflightgroup.slack.com/archives/C3D7R2J0P/p1608487449360200).

### Pins

With a bit of grepping, we can track where a pin appears in the source. E.g. pin PE13 is found in the following places relevant to an F7 board (like the one used above):

    src/main/target/NUCLEOF722/target.h:#define SPI4_MISO_PIN PE13

    src/main/drivers/io_def_generated.h:# define DEFIO_TAG__PE13 DEFIO_TAG_MAKE(DEFIO_GPIOID__E, 13)
    src/main/drivers/io_def_generated.h:# define DEFIO_TAG_E__PE13 DEFIO_TAG_MAKE(DEFIO_GPIOID__E, 13)
    src/main/drivers/io_def_generated.h:# define DEFIO_REC__PE13 DEFIO_REC_INDEXED(BITCOUNT(DEFIO_PORT...

    src/main/drivers/timer_stm32f7xx.c: DEF_TIM(TIM1, CH3, PE13, TIM_USE_ANY, 0, 0),
    src/main/drivers/bus_spi_pinconfig.c: { DEFIO_TAG_E(PE13), GPIO_AF5_SPI4 },
    src/main/drivers/timer_def.h:#define DEF_TIM_AF__PE13__TCH_TIM1_CH3 D(1, 1)

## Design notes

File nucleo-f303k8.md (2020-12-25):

Nucleo F303K8 first steps
=========================

Power board via USB. The board comes with an example program that gently flashes the green user LED. Remove the jumper that's connecting pins GND and D2 and the green LED will flash faster.

**Important:** remove this jumper now - it's only there for use in the demo program and it's very important that it not be present and accidentally short D2 when it's used for other purposes later.

Update ST-LINK firmware:

    $ sudo .../bin/java -jar STLinkUpgrade.jar

Downloaded [STM32CubeIDE](https://www.st.com/en/development-tools/stm32cubeide.html) and:

    $ cd ~/Downloads
    $ unzip en.en-st-stm32cubeide_1-5-0_8698_20201117_1050_amd64-deb_bundle_sh.zip
    $ chmod 755 st-stm32cubeide_1.5.0_8698_20201117_1050_amd64.deb_bundle.sh
    $ sudo ./st-stm32cubeide_1.5.0_8698_20201117_1050_amd64.deb_bundle.sh

In addition to installing standard Ubuntu packages (like Java), it also installs:

    $ dpkg-query -L segger-jlink-udev-rules
    /etc/udev/rules.d/99-jlink.rules
    
    $ dpkg-query -L st-stlink-udev-rules
    /etc/udev/rules.d/49-stlinkv1.rules
    /etc/udev/rules.d/49-stlinkv3.rules
    /etc/udev/rules.d/49-stlinkv2.rules
    /etc/udev/rules.d/49-stlinkv2-1.rules

    $ dpkg-query -L st-stlink-server
    /usr/bin/stlink-server

    $ dpkg-query -L st-stm32cubeide-1.5.0
    ...
    /opt/st/stm32cubeide_1.5.0/stm32cubeide
    ...

Note: the J-Link `udev` rules overlapped with my existing MBED CMSIS-DAP rules but didn't contradict or override anything. The ST-LINK rules didn't overlap with any of my existing rules.

Then I launched it:

    $ /opt/st/stm32cubeide_1.5.0/stm32cubeide

This starts an Eclipse based IDE. I closed the introductory pane (after checking out the minimalist _Getting Started_ guide) and selected _Create a NEW STM32 project_.

It took a little while to get started, then I switched from _MCU/MPU Selector_ to _Board Selector_ and filtered for _F303K8_ under _Part Number_ and selected the single matching result.

I chose "f303k8-usb" as the project name and C++ as the targeted language.

It created a project that, among other things, included an `.ioc` file which it opened as the main pane - this consisted of a pinout for the F303K8 processor.

It was only at this point that I realized that the STM32F303K8, used on this board, does not support USB - unlike the STM32F303RE used on the larger Nucleo-64 board (compare the communication interfaces mentioned for the STM32F303RE [here](https://www.st.com/en/microcontrollers-microprocessors/stm32f303re.html) and those for the STM32F303K8 [here](https://www.st.com/en/microcontrollers-microprocessors/stm32f303k8.html)).

So I wouldn't be able to set up USB virtual COM port as outlined in this [guide](https://shawnhymel.com/1795/getting-started-with-stm32-nucleo-usb-virtual-com-port/) (and about which, I asked this StackExchange [question](https://electronics.stackexchange.com/q/539117/27099)).

Having said that, it's clear from the pinout that USART2 (PA2 and PA15) is assigned to a virtual com port (VCP). And this VCP is accessible via the ST-LINK.

So I set about getting to a point where I output `1` to USART1 and `2` to USART2 every second and then investigated how I could access these UARTs from my PC.

This proved to be very easy:

* I created a new STM32 project called "f303k8-uarts" and let it _Initialize all peripherals with their default Mode_ when asked.
* Then in the `.ioc` pane, I went to _Connectivity_. _USART2_ was already selected - if you click on it you can see its configuration, including the fact that its mode is _Asynchronous_ and its baud rate is 38.4kbps.
* I then clicked on _USART1_ and under its configuration, set mode to _Asynchronous_ as well. In the pinout diagram, I could see that its pins were PA9 (TX) and PA10 (RX).
* Then I selected _File_ / _Save_ and selected _Yes_ when asked _Do you want to generate Code?_
* Then in the _Project Explorer_, I went to _Core_ / _Src_ and opened `main.c`. It's worth taking a quick look through this skeleton.
* I went to the `while` loop and added...

```
int ch1 = '1';
int ch2 = '2';

HAL_UART_Transmit(&huart1, (uint8_t *)&ch1, 1, 0xFFFF);
HAL_UART_Transmit(&huart2, (uint8_t *)&ch2, 1, 0xFFFF);
HAL_Delay(1000);
```

The `HAL_UART_Transmit` and `HAL_Delay` functions were discovered after a few seconds googling "stm32cubemx uart example".

Then I went to _Project_ / _Build All_, followed by _Run_ / _Debug As_ and selected _STM32 Cortex-M C/C++ Application_. There was no additional setup that needed to done under any of the tabs of the resulting launch configuration. It automatically builds the project (so _Build All_ was unnecessary), downloads it to the target and stops on the first line of the `main` function.

After stepping through the `while` loop once, I let it run (i.e. _Resume_). Having determined that `ttyACM0` corresponded to the VCP created by the ST-LINK, I could connect to UART2:

    $ screen /dev/ttyACM0 38400
    2222...

Use `crtl-A` followed by `\` to exit `screen`.

Note: the RGB LED beside the USB connector on the board flashes continuously in debug mode and is a less distracting solid red in non-debug mode.

I then used a 3.3V USB-to-serial cable (like this [one](https://www.sparkfun.com/products/12977) from SparkFun or this [one](https://www.adafruit.com/product/954) from Adafruit).

If you look at the pinout diagram that came with in Nucleo board's blister pack, you'll see PA9 and PA10 at the upper-left, i.e. the two pins we saw above for _USART1_. Below them is the reset pin NRST and a GND pin.

So I connected the ground pin on the cable to the GND pin on the board and connected the RX and TX pins of the cable to PA9 and PA10 without making any effort to check which should go to which. Leave the 5V pin of the cable unconnected.

Having determined that `ttyUSB0` corresponed to the USB-to-serial cable, I could connect to UART1:

    $ screen /dev/ttyUSB0 38400

No data appeared, so I swapped the RX and TX pins and tried again:

    $ screen /dev/ttyUSB0 38400
    1111...

Aside: I actually used an [Olimex USB serial cable F](https://www.olimex.com/Products/Components/Cables/USB-Serial-Cable/USB-Serial-Cable-F/) which doesn't bother with a 5V pin.

So that was it, I could access UART1 and UART2 and from the `.ioc` pinout diagram and I could see that:

* UART1 has PA9 (TX) and PA10 (RX).
* UART2 has PA2 (TX) and PA15 (RX).

Note: the F303K8 [overview page](https://www.st.com/en/microcontrollers-microprocessors/stm32f303k8.html#overview) says that it can have "up to three USARTs" but its clear from the [reference manual](https://www.st.com/resource/en/datasheet/stm32f303k8.pdf) that, while this statememnt applies for processors in the F303 range, the F303K8 has only two USARTs.

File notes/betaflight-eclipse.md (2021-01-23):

Working with Betaflight in Eclipse
==================================

Download the Eclipse IDE for Embedded C/C++ Developers as covered [here](https://eclipse-embed-cdt.github.io/plugins/install/).

    $ tar -xf ~/Downloads/eclipse-embedcdt-2020-09-R-linux.gtk.x86_64.tar.gz 
    $ mv eclipse eclipse-embedcdt-2020-09-R
    $ cd eclipse-embedcdt-2020-09-R
    $ ./eclipse

Import the checked out Betaflight repository - _File_ / _New_ / _Makefile Project with Existing Code_ - choose a _Project Name_, e.g. "betaflight", specify the location and select _Arm Cross GCC_ as the toolchain.

Go to _Project_ / _Properties_, then _C/C++ Build_ and select the _Behavior_ tab.

Change the _Build (incremental build)_ from _all_ to _TARGET=NUCLEOF722_ (replacing _NUCLEOF722_ with your desired target).

TODO: actually, you should set _TARGET_ as an environment variable and _hex_ as the target.

Expand _C/C++ Build_ and select _Settings_, under _Toolchains_, select _GNU Tools for Arm Embedded Processors_.

Note: _GNU Tools for Arm Embedded Processors_ seems to have been the name used up to and including 9-2019-q4-major in the release notes. After that they just call it _GNU Arm Embedded Toolchain_.

Note: the default is to use a toolchain installed using [xPack](https://xpack.github.io/). This seems to be the Eclipse project's preferred way to manage toolchains for cross platform projects. To install the _GNU Arm Embedded GCC binaries_ xPack see [here](https://xpack.github.io/arm-none-eabi-gcc/install/). I chose instead to use the toolchain installed by the Ubuntu `gcc-arm-none-eabi` package.

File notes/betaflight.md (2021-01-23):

Notes on working with Betaflight
================================

The following page contains various notes accumulated while working on Betaflight

Branches
--------

Your primary Betaflight branches are:

* [4.2.5-nucleof722_min-redux](https://github.com/george-hawkins/betaflight/tree/4.2.5-nucleof722_min-redux) - where you've cleaned up things and just have a minimalist `NUCLEOF722_MIN` target along with a couple of minor bugfixes (related to things not compiling if certain features are undefined) and your support for booting into pit mode and supporting the non-standard Eachine TX805 pit mode behavior.
* [4.2.5-nucleof722_min](https://github.com/george-hawkins/betaflight/commits/4.2.5-nucleof722_min) - where you worked previously on creating the minimal target and tried out a few experimental features (like disabling VCP) which are discussed below but not included in 4.2.5-nucleof722_min-redux.

See [`NUCLEOF722_MIN/target.h`](https://github.com/george-hawkins/betaflight/blob/4.2.5-nucleof722_min-redux/src/main/target/NUCLEOF722_MIN/target.h) for my comprehensive minimalist `target.h` for the Nucleo-F722ZE board. Add see [`cli-diff-all.txt`](https://github.com/george-hawkins/betaflight/blob/4.2.5-nucleof722_min-redux/cli-diff-all.txt) for the settings file to with it.

I tried to get my change, to configure booting into pit mode, accepted by Betaflight (see [here](https://github.com/betaflight/betaflight/pull/10432)) but it's not currently considered acceptably generic in its present form.

Note: I've got a gist [here](https://gist.github.com/george-hawkins/9fbf557a41dcb063c480cd9152de6d32) that covers how Betaflight works with SmartAudio using `saSetMode`, `saQueueCmd` and various flags.

I also submitted by TX805 changes as a _draft_ PR [here](https://github.com/betaflight/betaflight/pull/10436). I also announced it [here](https://intofpv.com/t-betaflight-fix-for-toggling-pit-mode-via-tx-and-configurator?pid=124171) on InfoFPV but didn't get enough interest to feel it worth pushing (given that the Betaflight people are unwilling to incorporate product specific workarounds).

Space savings from undefining features
--------------------------------------

In `NUCLEOF722_MIN/target.h` there are comments that indicate the space saving gained by undefining various macro values, e.g. `USE_CLI`. These savings aren't independant, e.g. some macros enable whole areas of functionality while others just enable certain sections within those areas of functionality. But despite this, the numbers shown in `target.h` give some indication of the space savings possible.

Most of this information was gathered in a sequence of automated experiments on undefining a large number or macros, either individually or cummulatively. The results of these experiments are summarized in [`size-costs.md`](size-costs.md).

A few additional relevant macros were found after these experiments but nearly all were covered.

Working with Betaflight in the Eclipse IDE for Embedded C/C++ Developers
------------------------------------------------------------------------

I did almost all my work with Betaflight in `vim`. I took a start at getting it working with the version of the Eclipse IDE intended for embedded C/C++ developers - the relevant notes are in [`betaflight-eclipse.md`](betaflight-eclipse.md).

Basic steps when working with the Nucleo-F722ZE
-----------------------------------------------

Copy the existing target:

```
$ cp -r src/main/target/NUCLEOF722 src/main/target/NUCLEOF722_MIN
```

Modify the `target.h` file:

```
$ vi src/main/target/NUCLEOF722_MIN/target.h
```

Build the target:

```
$ rm obj/*.hex; make hex TARGET=NUCLEOF722_MIN
```

Copy the `.hex` file to the board:

```
$ cp obj/*.hex /media/$USER/NODE_F722ZE
```

List the sizes of functions and objects with static storage to get a handle on what's taking up space:

```
$ arm-none-eabi-nm --print-size --size-sort obj/main/betaflight_NUCLEOF722_MIN.elf
```

Run the Configurator:

```
$ /opt/betaflight/betaflight-configurator/betaflight-configurator
```

Valid UART pins
---------------

Oddly, the NUCLEOF722 `target.h` defines invalid pins for UART3 (see [here](https://github.com/betaflight/betaflight/blob/4.2.5/src/main/target/NUCLEOF722/target.h#L82)).

So what are valid pins? It turns out that the easiest place to find these is in [`drivers/serial_uart_stm32f7xx.c`](https://github.com/betaflight/betaflight/blob/4.2.5/src/main/drivers/serial_uart_stm32f7xx.c). E.g. there you can see that PA9 or PB6 can be used for the TX pin for UART1.

I tried out all the combinations possible for pins that are exposed via the Nucleo board's Zio headers. All expected combinations (except one) worked - the valid Zio accessible combinations are as follows:

* `UART1_TX_PIN` PB6
* `UART1_RX_PIN` NONE
* `UART2_RX_PIN` PD6 / PA3
* `UART2_TX_PIN` PD5
* `UART3_TX_PIN` PB10 / PC10
* `UART3_RX_PIN` PB11 / PC11
* `UART4_TX_PIN` PC10 / PA0
* `UART4_RX_PIN` PC11
* `UART5_TX_PIN` PC12
* `UART5_RX_PIN` PD2
* `UART6_TX_PIN` PC6
* `UART6_RX_PIN` PC7
* `UART7_TX_PIN` PE8 / PF7
* `UART7_RX_PIN` PE7
* `UART8_TX_PIN` NONE
* `UART8_RX_PIN` PE0

The pair that didn't work was:

* `UART6_TX_PIN` PG14
* `UART6_RX_PIN` PG9

To use G pins at all, you have to a definition for `TARGET_IO_PORTG` to `target.h` (in addition to the existing definitions for ports A to F) otherwise compilation fails. But evidently more is still required - I suspect this isn't anything fundamental and simply that G pins are not used (no other target currently specifies a G pin for anything) and so some minor setup has been missed out for G.

For more on the UART pins (not just those above that are accessible via the Zio headers), see [`f722ze-uart-pins.md`](f722ze-uart-pins.md).

Note: like `timerHardware` (discussed below), if you add or remove UARTs or change their pin assignments then you have to reset all settings, after flashing the new firmware, before these changes will show up in the Configurator.

I eventually settled on definitions for pins for four hardware UARTs. Many pins can be used for different purposes, e.g. UART, SPI etc. So I looked at which UARTs and which pin combinations are most commonly seen in the existing targets and chose the 4 most popular pairs on the basis that these pairs are unlikely to clash with some other common popular use for a given pin. Interestingly, UARTs 1 and 2 are far less commonly used that UARTs 3 to 6. I thought initially this might be because UARTs 1 and 2 are typically hardwired to other devices on the flight controller but even if these UARTs aren't available for end-users to use they still have to be defined for use in Betaflight. I guess it maybe reflects something to do with what devices are exposed on the low pin-count packages, like LQFP64, typically used in flight controllers, i.e. maybe UARTs 1 and 2 aren't exposed on these chips. Or maybe it reflects the fact that the pins that can be used for UARTs 1 and 2 are more commonly already taken for some other purpose, e.g. SPI.

TODO: merge this section with the corresponding section in the main `README`.

Telemetry
---------

Telemetry isn't just for data like RSSI or temperature, it's also the channel via which the flight controller can communicate with your TX (and any Lua scripts running on it). It does this using the `USE_MSP_OVER_TELEMETRY` feature.

Initially, I thought MSP was coming in via the SBUS (as it comes in on an RX pin) and going out via SPORT (i.e. telemetry, as it goes out on a TX pin). But it turns out telemetry is a bi-directional half-duplex link and MSP works solely via telemetry (SBUS is not involved).

Even if you undefine every obvious telemetry related feature, the flight controller still report "Hdg" (heading) telemetry data and "Tmp1". If you want to remove "Hdg":

```
# telemetry_disabled_heading set to ON
# save
```

It turns out "Tmp1" isn't actually a real temperature but is being used to encode information about the flight controller state (see the `case FSSP_DATAID_T1` in `processSmartPortTelemetry` in [`telemetry/smartport.c`](https://github.com/betaflight/betaflight/blob/4.2.5/src/main/telemetry/smartport.c)). In OpenTX you see this sensor as something like "Tmp1 2002C", with the highest decimal place changing rapidly, it's actually a heartbeat value that's continously changing thru the values 1, 2 and 3 but encodes no meaning, the lower places do encode things, e.g. 2 at the end of 2002 means arming is disabled. If you want to remove "Tmp1":

```
# set telemetry_disabled_mode=ON
# save
```

To me `telemetry_disabled_mode` sounds dramatic but it really does just control if "Tmp1" (and under certain circumstances also "Tmp2") are sent.

Note: I thought MSP data must be similarly encoded into the data for a fake sensor but actually the SmartPort protocol supports different frame types - sensor data is sent with a `frameId` (see [`telemetry/smartport.c`](https://github.com/betaflight/betaflight/blob/4.2.5/src/main/telemetry/smartport.c) again) of `FSSP_DATA_FRAME` while MSP data comes in with a `frameId` of either `FSSP_MSPC_FRAME_SMARTPORT` or `FSSP_MSPC_FRAME_FPORT` and is sent out with a `frameId` of `FSSP_MSPS_FRAME`.

Debugging using tfp_printf
--------------------------

You can debug SmartAudio by adding the following define to `target.h`:

```
#define USE_SMARTAUDIO_DPRINTF
```

You should then check the value for `DPRINTF_SERIAL_PORT` in [`vtx_smartaudio.h`](https://github.com/betaflight/betaflight/blob/4.2.5/src/main/io/vtx_smartaudio.h). By default it's `SERIAL_PORT_USART3` but you can change it to something else if e.g. UART3 isn't available for some reason.

This then enables various debug output in the SmartAudio code that you can then view on the given UART using e.g. `screen`:

```
$ screen /dev/ttyUSB0 115200
```

Where `/dev/ttyUSB0` corresponds to the device created for your USB-to-serial cable that's connected to the relevant UART.

You can also use the same setup to add you're debug output, just add something like the following wherever you need:

```
tfp_printf("foo is set to %s", foo);
```

For more notes (than you want) on this, see [`smartaudio-debug.md`](smartaudio-debug.md).

Pin setup
---------

Certain pins can be associated with timers and this needs to be configured before such pins can e.g. be used for soft serial.

If you're using `USE_UNIFIED_TARGET` (along with `USE_TIMER_MGMT` and `USE_DMA_SPEC` which are defined by default for F4, F7 and H7 targets) then a `fullTimerHardware` array is defined for you, e.g. see [`drivers/timer_stm32f7xx.c`](https://github.com/betaflight/betaflight/blob/4.2.5/src/main/drivers/timer_stm32f7xx.c) for the full F7 table. If you look at the pins PA0 to PA15, you'll see that most of them can be used whereas if you look at the block PF0 to PF15, you'll see that only PF6 and PF7 can be associated with timers.

If you're not using `USE_UNIFIED_TARGET`, i.e. you've got your own custom board setup that goes beyond what can be configured via the CLI and needs its own entry under `src/main/targets`, then you have to define your own `timerHardware` table with entries for the pins you want to use for motors, PWM etc. (see the [`timerUsageFlag_e` enum](https://github.com/betaflight/betaflight/blob/4.2.5/src/main/drivers/timer.h#L54) in `timer.h`). These entries will show up when you enter `resource` in the CLI (unless you use `TIM_USE_ANY`, in which case the pin is ready for use but has to be actively assigned to something particular like a motor etc.).

See `target.c` and the other changes necessary to make a pin available for soft serial in commit [`7f63244`](https://github.com/george-hawkins/betaflight/commit/7f63244).

Note: `fullTimerHardware` specifies everything as `TIM_USE_ANY` and then it's up to you to assign pins to resources via the CLI, i.e. no pins are automatically assigned a purpose.

When creating an entry in your own `timerHardware`, just copy the definition for the pin that you're interested in from `fullTimerHardware`, you can change the usage value from `TIM_USE_ANY` if you want but leave the other values as they are.

If you look carefully, you'll see certain pins defined in `fullTimerHardware` more than once, e.g. PA2 appears three times but each time with a different timer and channel channel combination. I'm not sure what rules you should apply when choosing which definiting to copy when copying such definitions into your own `timerHardware`, e.g. if I look existing targets it _looks_ like people try to choose different channels for the different motors (but the timers don't have to be different). And what happens where you're using a unified target? Via the CLI, you can't say you want the first, second or third definition of e.g. PA2 if you want to assign it to a resource.

It's clear that pins that you intend to use for the usages covered by `timerUsageFlag_e`, i.e. motors etc., need to be defined in `timerHardware`. But for other purposes, one has to work out if an entry is needed or not, e.g. hardware UART pins should not have an entry but pins that you plan to use for soft serial must have an entry (you can specify them as `TIM_USE_ANY` or steal a pin specified for another purpose, e.g. `TIM_USE_PPM`).

Important: when I modified the `timerHardware` table or the related defines here, I really had to reset all settings and then reload a backup (created previously with `diff all`), taking care that the modifications hadn't affected the validity of any of the commands, e.g.:

* If you'd had six motor entries previously and then reduced them to four then any resource command that attempted to release the 6th motor pin for some other use would fail.
* The first `TIM_USE_MOTOR` motor entry in `timerHardware` becomes `resource MOTOR 1` and so on, so changing the order of things in `timerHardware` or knocking out entries affects which pins get assigned to which motor number.

For some more details, see this [question](https://betaflightgroup.slack.com/archives/C3D7R2J0P/p1610196502089800) that I asked on the Betaflight #support Slack channel.

Configuring soft serial pins in code
------------------------------------

In order for a soft serial port to show up in the Configurator, you have to assign at least one pin to it.

You can do this in the CLI, as outlined in the main `README`, like so:

    resource SERIAL_TX 11 B04

Or you can configure a specific pin in `target.h` like so:

```
#define USE_SOFTSERIAL1
#define SOFTSERIAL1_TX_PIN PB4
```

Eliminating the VCP
-------------------

If you've already undefined `USE_USB_CDC_HID` then you can save a significant amount of space by disabling VCP and so removing the need for any USB related support. VCP is the virtual com port behind the USB connection that the Configurator usually uses to talk to a board.

You can instead use a real UART on the board and connect it up to your computer with a [USB-to-serial cable](https://www.adafruit.com/product/954).

It's simple to disable VCP - you just undefine `USE_VCP`. However, if you just do this and switch from a firmware with VCP enabled to one without then things get a little strange. If you don't take care then the board gets confused about how to interpret its existing UART configuration, now that the first port (the VCP port) is gone, and you essentially end up bricking the device.

If you get into a situation where you can't connect to the board anymore do a full chip erase with STM32CubeProgrammer (covered elsewhere) and then copy on a firmware with VCP enabled.

Initially, I thought the issue was that with the first port disappearing, the pins in the existing configuration were being assigned to the wrong ports, e.g. those of the first port were being assigned to what had been the second port but was now the first port. So to keep things aligned I set things up like this:

    #ifndef USE_VCP
    #define USE_UART1
    #define UART1_TX_PIN PB6
    #endif

I.e. `USE_UART1` was only defined if `USE_VCP` was not and so would pop into existence as the first port when the VCP port disappeared and so keep the underlying pin configuration aligned as far as the other ports were concerned.

    // If using USE_SOFTSERIAL1 and/or USE_SOFTSERIAL2, each counts towards the port count.
    #ifdef USE_VCP
    #define USE_USB_DETECT
    #define USB_DETECT_PIN PA9
    #define SERIAL_PORT_COUNT 5 // VCP, USART3, UART4, UART5, UART6
    #else
    #define SERIAL_PORT_COUNT 4 // USART3, UART4, UART5, UART6
    #define USE_TARGET_CONFIG // Enable specifying MSP port in config.c
    #endif

So it's as simple as adjusting `SERIAL_PORT_COUNT` to reflect the disappearance of the VCP port. Before undefining `USE_VCP` you need to have configure the real UART, that you intend to connect to your computer, to use MSP (via the _Ports_ tab in the Configurator). MSP is the protocol that the Configurator uses to talk with the board. Test that you can now also connect via your USB-to-serial cable. Then update the firmware with a firmware where the only difference is that `USE_VCP` has been undefined.

The port that you configured for MSP will continue to work after disabling. However, after connecting with the Configurator, you'll need to do a full reset of all setting to get all expected UARTs (for whatever reason the last one disappears). But this would also lose your MSP configuration for the real UART port that you're now using to connect to the board. This is where `USE_TARGET_CONFIG` (defined above) comes into play, using this and adding a `config.c` file you can hardcode that MSP be set for a particular UART on reset.

See commit [`435d954`](https://github.com/george-hawkins/betaflight/commit/435d954) for all the changes necessary, including the `config.c` file that sets things up.

Note: after a reset MSP is also automatically configured for the first UARTi so you can do without `USE_TARGET_CONFIG` and `config.c` if you're OK with having to use it for connecting from your computer.

Dual use UART
-------------

If you've disabled VCP and are using a real UART to connect to the Configurator then you can imagine a situation where you're so short on UARTs that you'd like the UART used for the Configurator to be useable for something else when not using the Configurator (i.e. the normal case - in the life of a flight controller one connects it to the Configurator relatively rarely).

E.g. it might be nice to use the UART that you usually use for SmartAudio for the Configurator when necessary (and keep the VTX powered down in these situations).

The solution, I came up with for this was to define an additional UART in `target.h` that used pins that weren't actually exposed by the flight controller (flight controllers tend to use the very low pin count MCU packages which means there are mean UART pins that don't actually have a corresponding physical pin).

So say this dummy UART is UART6, then it appears in the Configurator (even though the underlying pins aren't really available) and I can e.g. configure the MSP connection for the Configurator on a real UART, say UART3, and SmartAudio on the dummy UART6.

Then I can set things up such that if I short a particular GPIO pin on the board to ground, it will keep these settings, i.e. MSP on the real UART and SmartAudio on the dummy UART, but if I don't short the GPIO pin to ground then it will swap things such that SmartAudio gets the real UART and MSP the dummy.

So actively shorting the pin makes the flight controller ready for use on the bench with the Configurator and otherwise the Configurator UART can be used for something else, like SmartAudio.

You can see the necessary changes in commit [`9d8c73b`](https://github.com/george-hawkins/betaflight/commit/9d8c73b). Various targets already detect whether a paricular pin is shorted or not to determine the hardware revision of the board.

So I hijack this process and provide my own `detectHardwareRevision` that sets a global variable that can then be picked up in my own `targetPreInit` definition that swaps the ports an whether the global variable indicates the relevant GPIO pin (specified by `HW_PIN`) is low or not.

Then in the CLI the whole process has to be configured, e.g. like so:

    set serial_swap_ports_enabled=ON
    set serial_swap_ports=3,6

Note: I did have this working but there must be slightly more to it as you can't arbitrarily reassign pins, e.g. if you assign valid pins for UART3 to UART6 they won't work, you must use pins that are specified in the MCU datasheet for the UART. I any case if I was doing things again, I wouldn't go for this fancy setup with a dummy additional port and CLI settings like `serial_swap_ports`. I'd just hardcode things in `targetPreInit` to set a given UART to MSP under one condition and to SmartAudio, or whatever, under the other condition.

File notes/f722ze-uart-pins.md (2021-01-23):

F722ZE USART pins
=================

Pin information taken from the STM32F722ZE [datasheet](https://www.st.com/resource/en/datasheet/stm32f722ze.pdf):

* UART1_TX PA9/PB6
* UART2_TX PA2/PD5
* UART3_TX PB10/PC10/PD8
* UART4_TX PA0/PC10/PH13
* UART5_TX PC12
* UART6_TX PC6/PG14
* UART7_TX PE8/PF7
* UART8_TX PE1

* UART1_RX PA10/PB7
* UART2_RX PA3/PD6
* UART3_RX PB11/PC11/PD9
* UART4_RX PA1/PC11/PH14/PI9
* UART5_RX PD2
* UART6_RX PC7/PG9
* UART7_RX PE7/PF6
* UART8_RX PE0

It turns out it would have been much easier to find this information in [`drivers/serial_uart_stm32f7xx.c`](https://github.com/betaflight/betaflight/blob/4.2.5/src/main/drivers/serial_uart_stm32f7xx.c).

Notes:

* Yes - PC10 can be used by UART3_TX or UART4_TX and PC11 can be used by UART3_RX or UART4_RX.
* In most cases,the the RX pin is just after the TX pin, e.g. PA9 and PA10, but for some cases it's before, e.g. UART8, or there's no such relationship, e.g. UART5.
* It is not the case that where there seems to be an obvious pair, e.g. PA9 and PA10 for the TX and RX pins for UART1, that those pins have to be used in combination, e.g. PB7 is an alternative to PA10 and can be used just as well in combination with PA9.
* Most UARTs have as many options for the TX pin as the RX pin - this isn't the case for UART4.

UART pins on the Zio headers
----------------------------

The following UART pins are accessible via the Zio headers.

* UART1_TX PB6
* UART1_RX -

* UART2_TX PD5
* UART2_RX PA3/PD6

* UART3_TX PB10/PC10
* UART3_RX PB11/PC11

* UART4_TX PA0/PC10
* UART4_RX PC11

* UART5_TX PC12
* UART5_RX PD2

* UART6_TX PC6/PG14
* UART6_RX PC7/PG9

* UART7_TX PE8/PF7
* UART7_RX PE7

* UART8_TX -
* UART8_RX PE0

Pins PC10, PC11, PC12, PD2, PD5, PD6, PE0, PE7, PG9 and PG14, are not specified in `fullTimerHardware` in `src/main/drivers/timer_stm32f7xx.c`. I thought this _might_ be relevant but it is not. The `G` values may not be available until one defines `TARGET_IO_PORTG` in `target.h`.

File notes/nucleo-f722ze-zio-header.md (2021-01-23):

Nucleo-F722ZE Zio header pins
=============================

The Nucleo-F722ZE has two rows of female headers - these are called the Zio headers. Outside them are longer sets of plain thru-hole pins, i.e. without headers - these are called the morpho connectors.

This file lists the default pins on the Zio headers - some of these (as noted below) can be changed via solder bridges.

CN8
---

1 NC
3 IOREF
5 RESET - NRST
7 +3.3 V
9 +5 V
11 GND
13 GND
15 VIN

2 PC8
4 PC9
6 PC10
8 PC11
10 PC12
12 PD2
14 PG2
16 PG3

CN9
---

1 PA3
3 PC0
5 PC3
7 PF3
9 PF5
11 PF10
13 NC
15 NC
17 PF2
19 PF1
21 PF0
23 GND
25 PD0
27 PD1
29 PG0

Notes: pins 9 and 11 can be rooted thru instead to PB9 and PB8 respectively with SB138 and SB143.

2 PD7
4 PD6
6 PD5
8 PD4
10 PD3
12 GND
14 PE2
16 PE4
18 PE5
20 PE6
22 PE3
24 PF8
26 PF7
28 PF9
30 PG1

Notes: PE2 is connected to both CN9 pin 14 and CN10 pin 25. Only one must be used at any given time.

CN7
---

1 PC6
3 PB15
5 PB13
7 PB12
9 PA15
11 PC7
13 PB5
15 PB3
17 PA4
19 PB4

2 PB8
4 PB9
6 AREF
8 GND
10 PA5
12 PA6
14 PA7
16 PD14
18 PD15
20 PF12

Notes: pin 14 can be rooted thru instead to PB5 with SB121 and SB122.

CN10
----

1 AVDD
3 AGND
5 GND
7 PB1
9 PC2
11 PF4
13 PB6
15 PB2
17 GND
19 PD13
21 PD12
23 PD11
25 PE2
27 GND
29 PA0
31 PB0
33 PE0

2 PF13
4 PE9
6 PE11
8 PF14
10 PE13
12 PF15
14 PG14
16 PG9
18 PE8
20 PE7
22 GND
24 PE10
26 PE12
28 PE14
30 PE15
32 PB10
34 PB11

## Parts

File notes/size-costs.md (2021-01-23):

Size costs
==========

Build output:

       text	   data	    bss	    dec	    hex	filename
     347443	   5532	  56096	 409071	  63def	./obj/main/betaflight_NUCLEOF722_MIN.elf
    Creating HEX ./obj/betaflight_4.2.5_NUCLEOF722_MIN_norevision.hex

Total size without any undefines is 409071B. You can reduce this to just 129004B with all the undefines below, i.e. `USE_CLI` to `USE_TPA_MODE`.

All the following are gains made by using `#undef` in `target.h`.

`USE_CLI` has by far the largest impact. If you don't undefine `USE_CLI` you can still save 5196B with `#define MINIMAL_CLI`.

* 58723 USE_CLI
* 42261 USE_DSHOT
* 30810 USE_SERIAL_RX
* 24325 USE_CMS
* 18824 USE_TELEMETRY
* 17712 USE_OSD
* 15084 USE_BLACKBOX
* 11694 USE_VTX_COMMON
* 9133 USE_LED_STRIP_STATUS_MODE
* 7072 USE_GYRO_DATA_ANALYSE
* 7024 USE_RC_SMOOTHING_FILTER
* 5257 USE_SERVOS
* 2952 USE_GPS_UBLOX
* 2676 USE_SERIAL_4WAY_BLHELI_BOOTLOADER
* 2096 USE_GPS_NMEA
* 2024 USE_USB_CDC_HID
* 1845 USE_RCDEVICE
* 1784 USE_ITERM_RELAX
* 1680 USE_INTERPOLATED_SP
* 1473 USE_DYN_LPF
* 1468 USE_SERIAL_4WAY_SK_BOOTLOADER
* 1392 USE_D_MIN
* 1292 USE_BOARD_INFO
* 1264 USE_RUNAWAY_TAKEOFF
* 1136 USE_INTEGRATED_YAW_CONTROL

----

Each of the following gain you less than 1KiB on their own, all 22 together gain you only 9598B.

* 1002 USE_RTC_TIME
* 820 USE_PPM
* 820 USE_LAUNCH_CONTROL
* 804 USE_MULTI_GYRO
* 800 USE_TASK_STATISTICS
* 756 USE_BATTERY_VOLTAGE_SAG_COMPENSATION
* 744 USE_CAMERA_CONTROL
* 736 USE_UNCOMMON_MIXERS
* 496 USE_VIRTUAL_CURRENT_METER
* 416 USE_SERIALRX_SRXL2
* 388 USE_PERSISTENT_STATS
* 340 USE_GYRO_OVERFLOW_CHECK
* 280 USE_CUSTOM_BOX_NAMES
* 208 USE_THROTTLE_BOOST
* 204 USE_THRUST_LINEARIZATION
* 176 USE_MCO
* 156 USE_BRUSHED_ESC_AUTODETECT
* 136 USE_PIN_PULL_UP_DOWN
* 132 USE_GPS
* 120 USE_PINIOBOX
* 48 USE_MSP_DISPLAYPORT
* 16 USE_TPA_MODE

----

All of the following depend on something else to enabled before you get any gain.

They're ordered here by the size saving (see next section) they would have if undefined while everything else is left defined.

* 0 USE_VTX_CONTROL
* 0 USE_RPM_FILTER
* 0 USE_SERIALRX_SPEKTRUM
* 0 USE_DSHOT_BITBANG
* 0 USE_VTX_SMARTAUDIO
* 0 USE_SERIALRX_CRSF
* 0 USE_TELEMETRY_MAVLINK
* 0 USE_TELEMETRY_SRXL
* 0 USE_DSHOT_DMAR
* 0 USE_VTX_TABLE
* 0 USE_ESC_SENSOR
* 0 USE_EXTENDED_CMS_MENUS
* 0 USE_FRSKYOSD
* 0 USE_TELEMETRY_SMARTPORT
* 0 USE_TELEMETRY_CRSF
* 0 USE_SERIALRX_JETIEXBUS
* 0 USE_VTX_TRAMP
* 0 USE_TELEMETRY_HOTT
* 0 USE_SERIALRX_FPORT
* 0 USE_TELEMETRY_JETIEXBUS
* 0 USE_SERIALRX_IBUS
* 0 USE_MSP_OVER_TELEMETRY
* 0 USE_TELEMETRY_FRSKY_HUB
* 0 USE_TELEMETRY_IBUS
* 0 USE_SERIALRX_XBUS
* 0 USE_SERIALRX_SBUS
* 0 USE_DSHOT_TELEMETRY_STATS
* 0 USE_SIGNATURE
* 0 USE_SERIAL_PASSTHROUGH
* 0 USE_CRSF_CMS_TELEMETRY
* 0 USE_HOTT_TEXTMODE
* 0 USE_SPEKTRUM_BIND
* 0 USE_ABSOLUTE_CONTROL
* 0 USE_SERIALRX_SUMD
* 0 USE_SPEKTRUM_VTX_CONTROL
* 0 USE_ESC_SENSOR_INFO
* 0 USE_SPEKTRUM_CMS_TELEMETRY
* 0 USE_TELEMETRY_LTM
* 0 USE_OSD_ADJUSTMENTS
* 0 USE_OSD_PROFILES
* 0 USE_TELEMETRY_SENSORS_DISABLED_DETAILS
* 0 USE_ESC_SENSOR_TELEMETRY
* 0 USE_SPEKTRUM_VTX_TELEMETRY
* 0 USE_DYN_IDLE
* 0 USE_RX_LINK_QUALITY_INFO
* 0 USE_YAW_SPIN_RECOVERY
* 0 USE_PROFILE_NAMES
* 0 USE_CRSF_LINK_STATISTICS
* 0 USE_CLI_BATCH
* 0 USE_CMS_FAILSAFE_MENU
* 0 USE_OSD_STICK_OVERLAY
* 0 USE_RX_RSSI_DBM
* 0 USE_SPEKTRUM_REAL_RSSI
* 0 USE_VARIO
* 0 USE_SERIALRX_SUMH
* 0 USE_SENSOR_NAMES
* 0 USE_TELEMETRY_IBUS_EXTENDED
* 0 USE_OSD_OVER_MSP_DISPLAYPORT
* 0 USE_GYRO_REGISTER_DUMP
* 0 USE_SPEKTRUM_FAKE_RSSI
* 0 USE_CUSTOM_DEFAULTS_ADDRESS
* 0 USE_SPEKTRUM_BIND_PLUG
* 0 USE_GYRO_LPF2
* 0 USE_GYRO_DLPF_EXPERIMENTAL

----

If you just undefine one thing at a time you save the following per undefine:

53963 USE_CLI
45460 USE_DSHOT
34052 USE_SERIAL_RX
33287 USE_TELEMETRY
26392 USE_CMS
26036 USE_OSD
21066 USE_VTX_COMMON
21066 USE_VTX_CONTROL
13692 USE_BLACKBOX
13584 USE_LED_STRIP
11420 USE_RPM_FILTER
10408 USE_GYRO_DATA_ANALYSE
10164 USE_LED_STRIP_STATUS_MODE
8524 USE_SERIALRX_SPEKTRUM
8388 USE_DSHOT_BITBANG
7492 USE_VTX_SMARTAUDIO
6685 USE_SERVOS
6076 USE_SERIALRX_CRSF
5248 USE_TELEMETRY_MAVLINK
4956 USE_TELEMETRY_SRXL
4832 USE_DSHOT_DMAR
4732 USE_VTX_TABLE
4712 USE_ESC_SENSOR
4364 USE_EXTENDED_CMS_MENUS
4220 USE_FRSKYOSD
4192 USE_TELEMETRY_SMARTPORT
3704 USE_RC_SMOOTHING_FILTER
3684 USE_SERIALRX_SRXL2
3680 USE_TELEMETRY_CRSF
3236 USE_SERIALRX_JETIEXBUS
2964 USE_GPS_UBLOX
2852 USE_BOARD_INFO
2832 USE_VTX_TRAMP
2804 USE_TELEMETRY_HOTT
2716 USE_SERIALRX_FPORT
2496 USE_RTC_TIME
2492 USE_RCDEVICE
2456 USE_INTERPOLATED_SP
2404 USE_ITERM_RELAX
2364 USE_TELEMETRY_JETIEXBUS
2300 USE_SERIALRX_IBUS
2180 USE_USB_CDC_HID
2140 USE_MSP_OVER_TELEMETRY
2040 USE_TELEMETRY_FRSKY_HUB
1916 USE_LAUNCH_CONTROL
1804 USE_TELEMETRY_IBUS
1780 USE_GPS_NMEA
1728 USE_DYN_LPF
1696 USE_SERIAL_4WAY_SK_BOOTLOADER
1676 USE_SERIALRX_XBUS
1648 USE_SERIALRX_SBUS
1632 USE_DSHOT_TELEMETRY_STATS
1592 USE_D_MIN
1576 USE_TASK_STATISTICS
1556 USE_SERIAL_4WAY_BLHELI_BOOTLOADER
1472 USE_SIGNATURE
1448 USE_SERIAL_PASSTHROUGH
1432 USE_CRSF_CMS_TELEMETRY
1396 USE_RUNAWAY_TAKEOFF
1392 USE_HOTT_TEXTMODE
1384 USE_MULTI_GYRO
1272 USE_MSP_DISPLAYPORT
1272 USE_SPEKTRUM_BIND
1236 USE_ABSOLUTE_CONTROL
1216 USE_SERIALRX_SUMD
1136 USE_SPEKTRUM_VTX_CONTROL
1108 USE_ESC_SENSOR_INFO
1080 USE_SPEKTRUM_CMS_TELEMETRY
1064 USE_UNCOMMON_MIXERS
1056 USE_CAMERA_CONTROL
984 USE_TELEMETRY_LTM
960 USE_PERSISTENT_STATS
932 USE_THRUST_LINEARIZATION
888 USE_OSD_ADJUSTMENTS
864 USE_OSD_PROFILES
828 USE_PPM
792 USE_TELEMETRY_SENSORS_DISABLED_DETAILS
784 USE_ESC_SENSOR_TELEMETRY
724 USE_SPEKTRUM_VTX_TELEMETRY
716 USE_VIRTUAL_CURRENT_METER
708 USE_DYN_IDLE
700 USE_RX_LINK_QUALITY_INFO
680 USE_YAW_SPIN_RECOVERY
664 USE_PROFILE_NAMES
560 USE_CRSF_LINK_STATISTICS
548 USE_CLI_BATCH
528 USE_CMS_FAILSAFE_MENU
528 USE_OSD_STICK_OVERLAY
524 USE_GYRO_OVERFLOW_CHECK
488 USE_RX_RSSI_DBM
476 USE_BATTERY_VOLTAGE_SAG_COMPENSATION
472 USE_SPEKTRUM_REAL_RSSI
456 USE_CUSTOM_BOX_NAMES
436 USE_GPS
436 USE_VARIO
416 USE_PWM
388 USE_SERIALRX_SUMH
384 USE_SENSOR_NAMES
360 USE_THROTTLE_BOOST
328 USE_PINIOBOX
324 USE_INTEGRATED_YAW_CONTROL
312 USE_AIRMODE_LPF
268 USE_TELEMETRY_IBUS_EXTENDED
252 USE_OSD_OVER_MSP_DISPLAYPORT
232 USE_GYRO_REGISTER_DUMP
232 USE_RX_MSP
208 USE_PIN_PULL_UP_DOWN
204 USE_MCO
196 USE_SPEKTRUM_FAKE_RSSI
128 USE_BRUSHED_ESC_AUTODETECT
72 USE_CUSTOM_DEFAULTS_ADDRESS
64 USE_SPEKTRUM_BIND_PLUG
48 USE_TPA_MODE
32 USE_GYRO_LPF2
16 USE_GYRO_DLPF_EXPERIMENTAL

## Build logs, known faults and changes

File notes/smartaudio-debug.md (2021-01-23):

In `src/main/io/vtx_smartaudio.c` we find:

    debugSerialPort = openSerialPort(DPRINTF_SERIAL_PORT, FUNCTION_NONE, NULL, NULL, 115200, MODE_RXTX, 0);

So it opens `DPRINTF_SERIAL_PORT` at 115.2kpbs.

In `vtx_smartaudio.h` we find:

    #ifdef USE_SMARTAUDIO_DPRINTF
    #define DPRINTF_SERIAL_PORT SERIAL_PORT_USART3

And we can find `SERIAL_PORT_USART3` in `src/main/drivers/serial_pinconfig.c`:

    { SERIAL_PORT_USART3, IO_TAG(UART3_RX_PIN), IO_TAG(UART3_TX_PIN), IO_TAG(INVERTER_PIN_UART3) },

And in `src/main/target/NUCLEOF722/target.h` we find:

    #define UART3_RX_PIN PD9
    #define UART3_TX_PIN PD8

In the Nucleo-F77ZE manual we find:

> The USART3 interface available on PD8 and PD9 of the STM32 can be connected either to ST-LINK or to ST morpho connector.

So we should be able to access USART3 via the virtual com port (VCP) created for the ST-LINK.

Disappointingly, for reasons that are unclear to me, this wasn't the case.

So in Configurator, I toggled off _Serial Rx_ for _UART2_ and...

Added the following line to `src/main/target/NUCLEOF722/target.h`:

    #define USE_SMARTAUDIO_DPRINTF

And changed the line mentioned above in `src/main/io/vtx_smartaudio.h` that specified `SERIAL_PORT_USART3` to:

    #define DPRINTF_SERIAL_PORT SERIAL_PORT_USART2

Then I plugged in my 3.3V USB-to-serial cable, connecting its ground pin to one of the board GND pins and connecting RX and TX to PD6 and PD7, i.e. UART2, and:

    $ screen /dev/ttyUSB0 115200

I rebooted the board, nothing happened so I swapped RX and TX and tried again, this time things worked:

    $ screen /dev/ttyUSB0 115200
    smartAudioInit: OK
    vtxSmartAudioInit 1 power levels recorded
    smartAudioGetSettings
    process: sending queue
    received settings
    processResponse: rawPowerValue is 0, legacy power is 0
    processResponse: power changed from index 0 to index 1
    Current status: version: 2
      mode(0x10): fmode=chan pit=off  inb=off outb=off lock=unlocked deferred=off
      channel: 37 freq: 5865 power: 1 powerval: 0 pitfreq: 0 BootIntoPitMode: no 
    smartAudioSetFreq: GETPIT
    sainit: willBootIntoPitMode is false
    process: sending queue
    saProcessResponse: GETPIT freq 5300
    Current status: version: 2
      mode(0x10): fmode=chan pit=off  inb=off outb=off lock=unlocked deferred=off
      channel: 37 freq: 5865 power: 1 powerval: 0 pitfreq: 5300 BootIntoPitMode: no 
    process: sending status change polling
    smartAudioGetSettings
    received settings
    processResponse: rawPowerValue is 0, legacy power is 0
    process: sending status change polling
    smartAudioGetSettings
    received settings
    processResponse: rawPowerValue is 0, legacy power is 0
    process: sending status change polling
    smartAudioGetSettings
    received settings
    processResponse: rawPowerValue is 0, legacy power is 0
    process: sending status change polling
    smartAudioGetSettings
    received settings
    processResponse: rawPowerValue is 0, legacy power is 0
    process: sending status change polling
    smartAudioGetSettings
    received settings
    processResponse: rawPowerValue is 0, legacy power is 0
